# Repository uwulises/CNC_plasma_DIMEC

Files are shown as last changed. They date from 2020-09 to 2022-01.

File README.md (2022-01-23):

# Plasma CNC (LinuxCNC), Mechanical Engineering Department, Universidad de Chile [Currently on hiatus due to COVID-19].
Continuation of the development of a plasma CNC cutter.
Design based on https://www.precisionplasmallc.com/
- http://linuxcnc.org/2020/09/08/LinuxCNC-2.8.0/
- http://linuxcnc.org/docs/2.8/html/plasma/plasmac-user-guide_es.html (spanish version)
- http://linuxcnc.org/docs/devel/html/plasma/plasmac-user-guide.html

# CAD
Fusion 360 design https://a360.co/3tTwJg2

# Software
For this case, LinuxCNC V2.8 will be used, using a desktop computer with parallel port + optocoupler

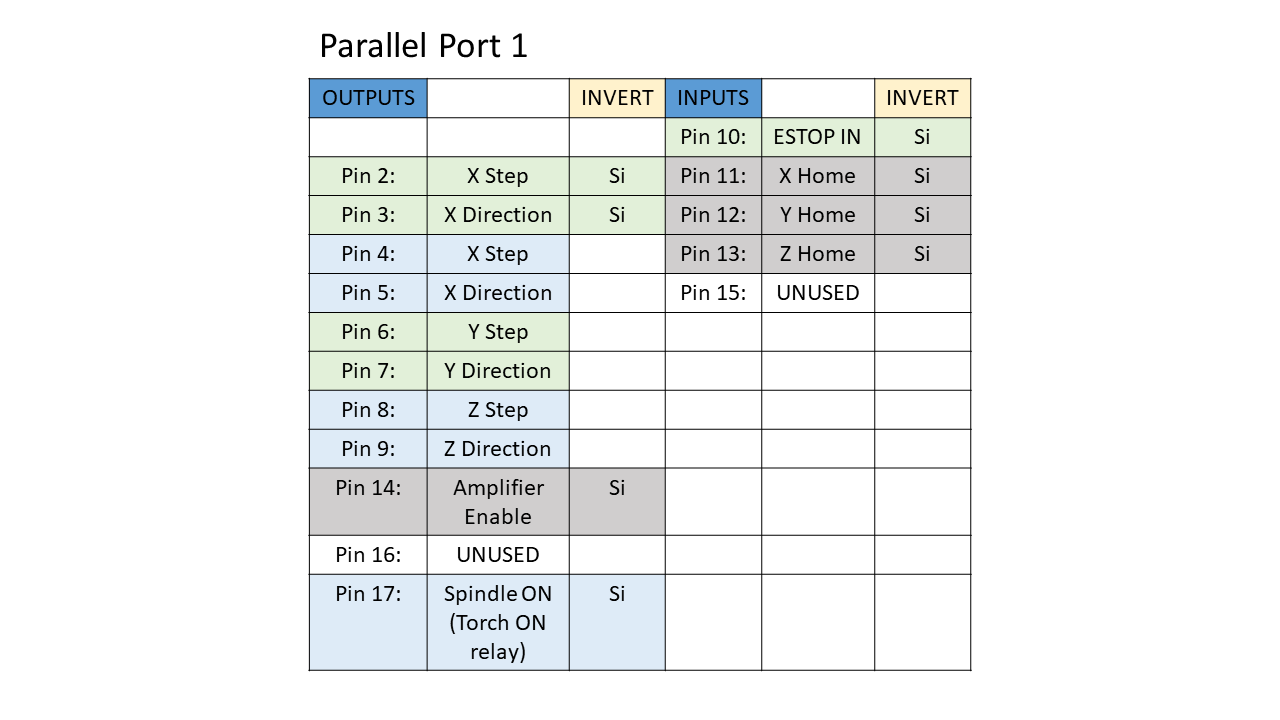
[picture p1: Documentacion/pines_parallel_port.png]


# Hardware
- Interface 5axis CNC
- Nema 23 HS45-4204S 3Nm 3A Stepper motors
- Driver DM556
- Timing Belt Pulley XL (14 & 44 teeth)
- Timing Belt 136 XL 10mm width
- Rack module 1.5 (X, Y axis)
- Gear module 1.5 20 teeth
- LJ12A3-4-Z/BX sensors (endstop)

# Electronics
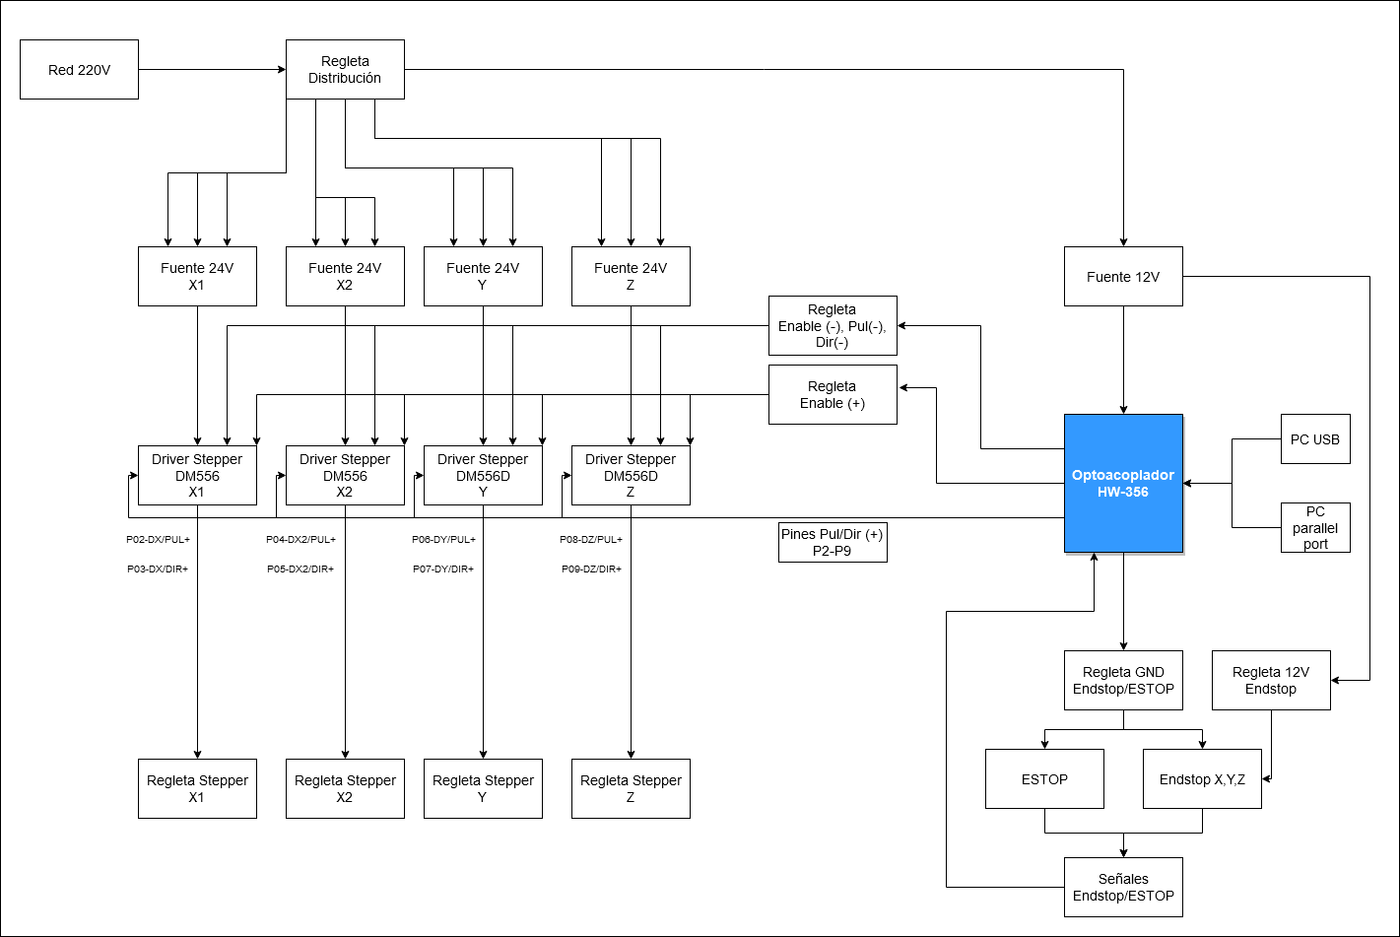
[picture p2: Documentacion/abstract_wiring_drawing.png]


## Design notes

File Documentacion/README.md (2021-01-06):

# Documentacion

- ME5601, old files from previous courses (Mechanical engineering students 2018)
- 5axis_CNC_interface, datasheet
- Informe electrico, old file from previous courses (Electrical engineering st 2018)
- Partes, BOM info

# Cableado



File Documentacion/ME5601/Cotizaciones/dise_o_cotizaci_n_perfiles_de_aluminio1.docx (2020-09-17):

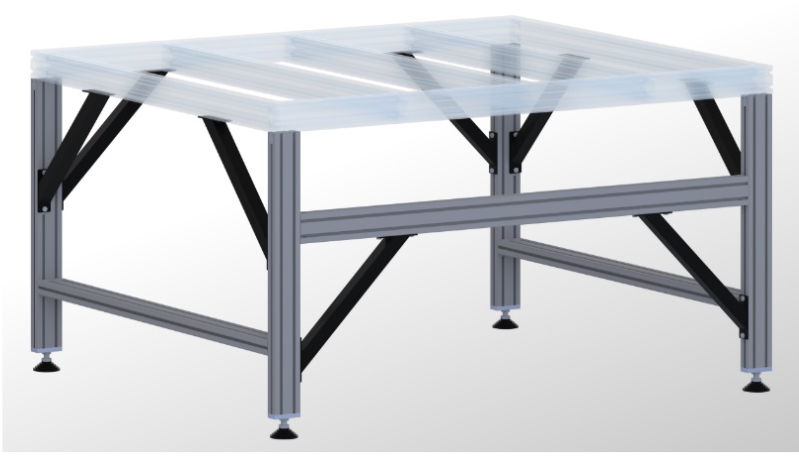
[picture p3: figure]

Cotización barras de aluminio de extrusión:

Para la mesa se consideró una forma de este tipo,con una superficie de 2,5mx2,5mx

Se encontraron 2 opciones viables, según el video: ttps://www.youtube.com/watch?v=ugjJXa6Sfl0

Para la realización de este tipo de mesa, se necesita:

N° | Pieza | dimensión | Precio [pesos] | cantidad | Total [pesos] | comentarios
1 | Marco extrusión simple 30X30mm | 30mmx30mmx1000mm | 6900 | 63 mts | 434700 | Se usan 2 barras de aluminio para mayor estabilidad en las patas como también para mayor precisión en los rieles
2 | Marco extrusión doble 20X40mm | 20mmx40mmx1000mm | 10135 | 31,5 mts | 319252,5 | Al ser doble, se puede ahorra en la cantidad de metros de material
3 | Placa unión* | variable | | 10 | | No se encontró precios de referencia, verificar precio
4 | Escuadras (union)** | 4 | 4990 | 4 | 19960
5 | Tornillo de nivelación | 4 | 1000 | 4 | 4000
6 | Barras diagonales | | aún por cotizar | 8
7 | M8 self aligning Roll-in T-nut | | 925 | 40 | 37016
8 | M8x30.00mm Socket Head Cap Screw (SHCS) | 30mm | 264,4 | 16 | 4230
9 | M6 x 14.00mm Socket Head Cap Screw (SHCS) | 14mm | 178,47 | 32 | 5711

*: Depende específicamente del diseño a utilizar, se puede hacer a la medida

**: la imagen de la escuadra es la que sigue y también se pueden realizar las uniones mediante placas adaptadas, por lo que no son del todo necesarias

Importar la mesa de 5’x10’ lista para su construcción cuesta: 874205,55 CLP (incluye costos de envío, además todas las uniones y un manual)

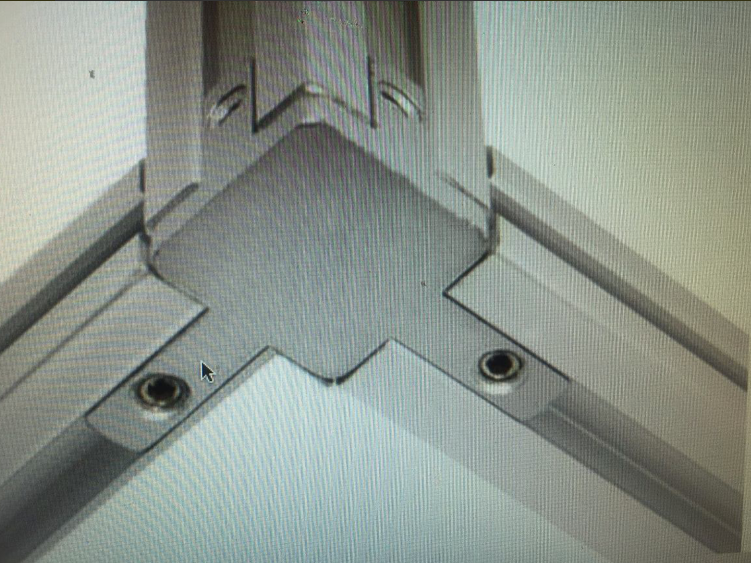
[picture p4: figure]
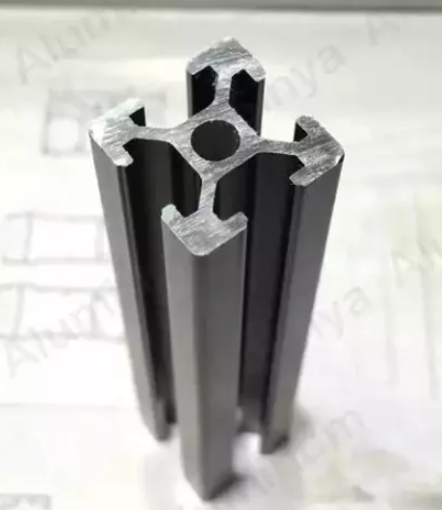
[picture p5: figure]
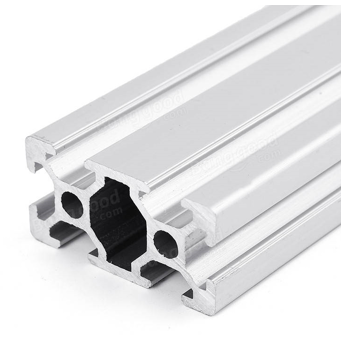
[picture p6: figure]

Figura 1. Escuadra (unión) Perfil simple Perfil Doble

Link precios marcos de extrusión:

Simple: https://articulo.mercadolibre.cl/MLC-450925992-perfil-aluminio-estructural-3030-6900-el-metro-mas-iva-_JM

Doble: https://www.banggood.com/es/Machifit-1000mm-Length-2040-T-Slot-Aluminum-Profiles-Extrusion-Frame-For-CNC-p-1264431.html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

Link detallado construcción mesa (todas sus piezas, pero otras dimensiones):

http://www.cncrouterparts.com/cad/2016Q4/CRP813-00-Leg-Kit-Plans_v2016Q4_1.pdf

Para el los tornillos con cabeza hexagonal, la cotización se realizo en :

https://8020.net/catalog/category/view/s/shop/id/837/?cat=469&p=3

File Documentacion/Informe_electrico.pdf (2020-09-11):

Universidad de Chile
Departamento de Ingeniería Eléctrica EL5004 - Taller de Diseño

# Informe Final

## CNC Plasma

### Profesores: Matías Mattamala Miguel Patiño

### Estudiantes: Juan Pablo Ruiz Felipe Salfate

Introducción | 3
Figura 1- Estructura del sistema de plasma CNC. | 3
Objetivo General | 3
Objetivos específicos | 4
Estructura del informe | 4
Especificaciones técnicas | 5
Alimentación | 5
Conexión con computador | 5
Requisitos de computador | 5
Hardware | 6
Descripción general de circuito de CNC | 6
Diagrama de módulos | 6
Consideraciones del computador | 7
Puerto paralelo | 7
Esquema de conector DB25 paralelo | 7
Tarjeta de optoacoplación de puerto paralelo de 5 ejes | 7
Pinout Tarjeta de optoacoplación de puerto paralelo | 8
Fuente de Poder | 8
Drivers | 8
Motores stepper | 9
Conmutación del Plasma | 9
Periféricos | 10
Placa de montaje | 10
Representación completa de placa de montaje | 11
Conexiones y bornes de tablero | 11
Elementos de construcción | 12
Placa de Montaje | 12
Automático | 12
Barra repartidora | 12
Bornes | 13
Regleta | 13
Riel Din | 13
Canaleta | 13
Botones de Emergencia | 14
Finales de Carrera | 14
Cableado | 14
Código de colores voltaje alto AC | 14
Código de colores voltaje medio DC | 14
Código de colores señales | 15
Conexiones y bornes de circuito en tablero | 15
Software | 16
Ejemplo de interfaz grafica de linuxCNC | 16
Instalación de Linux y Linux CNC | 16
Configuración LinuxCNC | 17
Configuraciones iniciales | 17
Valores CNC Plasma | 18
Prueba de Jitter | 19

Configuración puerto paralelo | 19
Configuración CNC Plasma | 20
Opciones de interfaz | 21
Configuracion ejes | 21
Encontrar velocidad máxima | 22
Encontrar aceleración máxima | 23
Valores CNC Plasma | 23
Uso de la interfaz | 23
Implementación y Resultados | 25
Resultados | 25
Prueba final de tablero en máquina | 25
Implementación lograda de placa de montaje | 26
Problemas | 26
Conclusiones | 27
Bibliografía | 28
Anexos | 29
Configuración Breakout Board CNC con Optoacoplación de 5 ejes | 29
Outputs de motores | 29
Inputs de señales | 29
Outputs de Señales | 30

## Introducción

El siguiente informe da cuenta del diseño y construcción realizado para la parte electrónica de la máquina CNC plasma, a ser construida en el taller Molina. Este informe tiene como objetivo dar cuenta del trabajo realizado durante el semestre, además de documentar sobre todos los aspectos del proyecto requeridos para poder ser finalizado, además de poder hacer reparaciones o modificaciones.

En la siguiente figura se puede ver el sistema implementado. Se comienza por el diseño de una pieza o corte en un sistema CAD externo cómo fusion 360 u otro, desde un equipo externo. Desde este se genera un código G, que describa la maquinación, el cual es interpretado por LinuxCNC, software instalado en la máquina que se preocupa de entregar las instrucciones a los componentes. Por medio de un cable paralelo, se envían las instrucciones a los drivers y al conmutador del plasma, pasando antes por un optoacoplador, que asegura la seguridad del computador ante una sobrecarga. Los drivers controlan los motores de la máquina, controlando así el movimiento del cabezal, mientras que el relé controla la antorcha plasma, cortando cuando sea requerido.

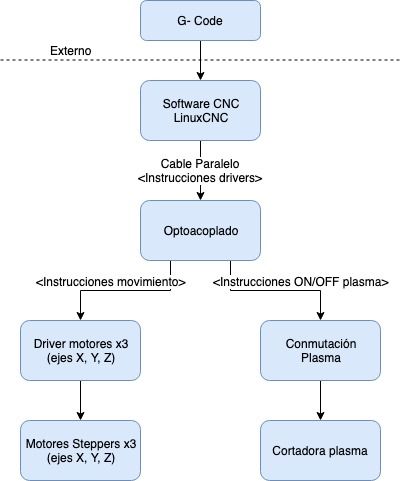
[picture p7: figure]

Figura 1- Estructura del sistema de plasma CNC.

## Objetivo General

Diseñar, implementar y testear la parte electrónica de una CNC plasma, incluyendo el control de los motores, el software CAM y los elementos electrónicos necesarios para su operación.

## Objetivos específicos

- Investigación, elección, instalación y configuración de un software CAM.
- Elección de un protocolo de comunicación entre computador y drivers.
- Diseño y construcción de tablero eléctrico, donde irán los componentes electrónicos y alimentación de la máquina.
- Diseño e implementación del cableado de la máquina.
- Testeo del correcto funcionamiento de la máquina.
- Documentación del proceso e implementación.

## Estructura del informe

Luego de introducido y el trabajo y sus objetivos, lo que sigue del informe comenzará por describir las especificaciones técnicas de diseño, seguido de distintas secciones, entregando información sobre distintos aspectos del proyecto. En la sección hardware se explicará todo lo referente al diseño e implementación de la placa de montaje. Del mismo modo, en la sección software se explicará LinuxCNC y su uso. Se continúa con los resultados obtenidos en la implementación y testeo para finalizar con un análisis del proceso y consideraciones futuras en las conclusiones.

## Especificaciones técnicas

Esta sección pretende ser un resumen de algunos aspectos técnicos importantes para una consulta más rápida del documento.

### Alimentación

El circuito se alimenta con 220 volts AC en red regular y con 5 volts DC por USB en el optoacoplador. El optoacoplador requiere ser alimentado tanto por 12V desde un transformador en la placa, como por 5V desde un cable USB.

### Conexión con computador

El optoacoplador de la placa se conecta usando un cable Db25 con un computador a través de puerto paralelo. Es importante asegurarse de que efectivamente el cable tenga todas las conexiones que debe tener, de otra manera el circuito no funciona.

### Requisitos de computador

La placa debería poder usarse con cualquier software CAM que funcione con puerto paralelo, es preferible usar un computador antiguo por temas de compatibilidad nativa. En este informe se expone el uso con LinuxCNC. Para este fin el computador debe tener un puerto paralelo instalado, una tarjeta de video para evitar retardos en el funcionamiento y linux instalado. Se expone en la sección correspondiente cómo realizar la instalación del software.

## Hardware

Se describen en esta sección todos los elementos eléctricos utilizados para el funcionamiento de la máquina. Se describe además, el diseño del tablero eléctrico implementado para la contención de todos los elementos necesarios, deteniéndose en aquellos elementos cuyo funcionamiento es importante para la operación de la máquina.

## Descripción general de circuito de CNC

El siguiente diagrama explica los módulos implementados para el funcionamiento del circuito. Existen dos tipos de conexiones importantes que tener en cuenta, las de alimentación y las de señal.

Comenzando por la alimentación del circuito, los elementos y conexiones que son de alta potencia (220V AC) están en rojo, las que son de potencia media (20-12 V DC) en amarillo y las conexiones de baja potencia (5 V DC) son verdes. Hay dos detalles importantes que tener en cuenta, en la etapa de alimentación de alta potencia, la fase pasa por un automático y un interruptor de emergencia, cosa de poder detener el circuito a tiempo en caso de cualquier problema. Además, el optoacoplador si bien tiene un puerto USB que debe ser conectado a una fuente para tener 5 V de referencia, no recibe la energía de ahí. Tiene su transformador propio de 12 volts con el cual se energiza.

Los nodos internos de control están en azul, las señales externas en blanco y los periféricos controlables en gris. El optoacoplador recibe señales desde los interruptores y el cable paralelo y envía señales hacia los drivers que controlan los motores, además de contar con un relé que puede ser usado para la conmutación del plasma. Los interruptores son energizados directamente desde el optoacoplador.

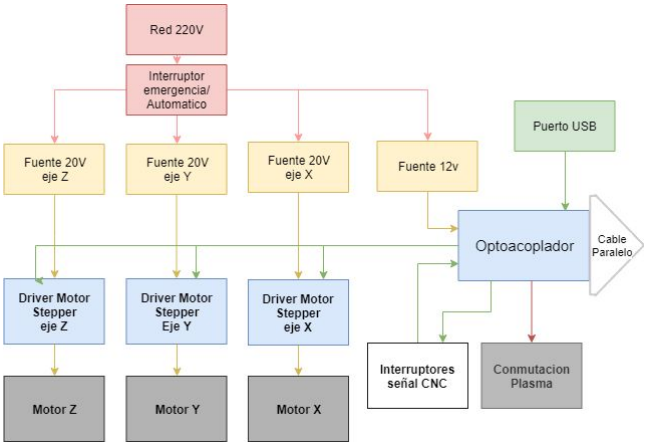
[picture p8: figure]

Diagrama de módulos

### Consideraciones del computador

LinuxCNC pide 2 elementos base para su funcionamiento, el primero es la presencia de un puerto paralelo, ya sea nativo o mediante una tarjeta, y el segundo es la presencia de una tarjeta de video para liberar de carga al procesador utilizado. En general el software va a funcionar mejor en computadores antiguos, además de requerir menos modificaciones (por lo general los computadores antiguos tenían puerto paralelo nativamente, cosa que ha desaparecido en los últimos años).

El sistema operativo elegido para operar es Linux, esto es importante por 3 razones. La primera suena bastante obvia, pero vale recalcar que LinuxCNC solo funciona en linux. Linux a diferencia de Windows es un sistema donde se permite nativamente la ejecución en tiempo real, en windows softwares cómo Mach3 necesitan driver especiales, que suelen tener conflictos con los computadores más modernos. Además, al ser un sistema altamente configurable, el desempeño de Linux en los computadores antiguos es bastante más fluido que el que puede tener Windows.

### Puerto paralelo

El puerto paralelo consiste en 25 canales de comunicación bidireccional, teniendo canales de entrada, salida y tierra, que pueden ser usado para la comunicación con periféricos por medio de un puerto PCI. Antiguamente era el medio estándar para la comunicación con impresoras, sin embargo el USB quitó su lugar, al ser más cómodo y barato. Pese a esto, el USB es solo comunicación serial, siendo más lento que el cable paralelo, teniéndose que en máquinas CNC, la velocidad de comunicación es clave.

Para la conexión de linuxCNC con cualquier máquina CNC, se requiere de un cable de puerto paralelo DB25. Es inmensamente importante tener cuidado al momento de comprar el cable, comprobando que efectivamente sea un DB25, el cual tiene todas sus pines conectados. Es más común encontrar cables de impresora que trae varios pines sin conexión, no siendo necesarios para el control de impresoras, abaratando costos en el proceso.

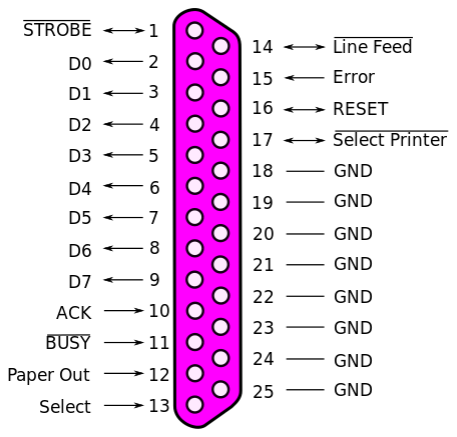
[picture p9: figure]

Esquema de conector DB25 paralelo

### Tarjeta de optoacoplación de puerto paralelo de 5 ejes

Se hizo uso de una tarjeta idéntica a la de la figura para la optoacoplación . Esta se conecta al

1
computador mediante un conector DB25 y se alimenta mediante USB. Se puede alimentar con una fuente de 12 a 24V, sin embargo se sigue requiriendo la conexión USB para funcionar. Permite transmitir hacia el computador 5 señales, siendo parada de emergencia y límites de ejes X, Y y Z, y desde el computador, las señales de control de hasta 5 drivers, un control optoacoplado de motor de

1 Se trata de un modelo Chino del cual la documentación es difusa, pero se adjunta en anexos.

hasta 10 volts en PWM (solo si recibe alimentación extra) y un relay configurable mediante un jumper. En caso de que se configure el relé, el eje B (5to eje) no puede ser usado.

Según el manual del optoacoplador, la conexión del relé se hace en el pin de B Dir, sin embargo en algunos lugares se menciona que esto debe ser realizado en la interfaz ON/OFF del Spindle. La conexión correcta no pudo ser corroborado.

Pinout Tarjeta de optoacoplación de puerto paralelo

### Fuente de Poder

Todas las fuentes escogidas son switching de voltaje constante. Se tienen 3 de 20 Volts para los drivers y 1 para el optoacoplador. Este último, si bien obtiene su energía en mayor parte de la fuente de poder, debe ser conectado por USB a un computador para tener 5 Volts de referencia. La falta de esto deja a la fuente sin la polarización necesaria para operar correctamente, e inhibe el correcto funcionamiento del circuito. En aplicaciones de poca potencia es posible usar el optoacoplador solo haciendo uso del USB, dejando a la fuente de 12 volts cómo opcional.

En cuanto a los drivers, se usa una fuente de poder para cada eje, cosa de asegurar mayor robustez ante los fallos. El uso de solo una fuente podría funcionar bien en aplicaciones de poca potencia, pero en las pruebas con un stepper nema 23 se llegó a ver voltajes cercanos a los 100 volts en la salida del driver, cosa que prueba la potencia que puede llegar a exigir ciertos motores.

### Drivers

Para poder controlar un motor stepper se pueden utilizar drivers especializados para ello. Con el driver se puede controlar la intensidad, dirección y habilidad o desabilidad el motor, además de poder conseguir una mayor definición de giro con micro-pasos.

El driver recibe como entrada 3 señales, Dir, Pul y Enable. Con Dir se controla la dirección de giro del motor, con Pul se envía un tren de pulsos según los cuales gira el motor y Enable sirve como un pin de control.

El driver recibe la alimentación de los motores y la conexión con los ejes A y B del motor, con los cuales puede energizar y controlar el motor.

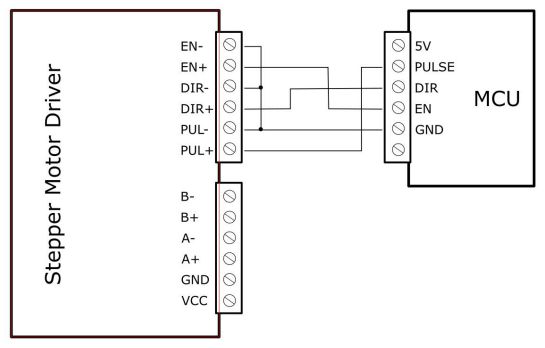
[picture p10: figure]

Al conectar el driver existen 2 configuraciones, ánodo común, en donde todos los polos positivos de control se conectan juntos a un voltaje positivo, y cátodo común, en donde todos los polos negativos de control se conectan a tierra. Los polos opuestos se conectan a las respectivas señales de Dir, Pul y Enable. Las características producto del tipo de conexión que se haga dependerá del driver que se esté utilizando.

Los drivers a utilizar en la versión final son los DM556, sin embargo, debido a que no se contó con su disponibilidad, se utilizó el driver DM860 para las pruebas.

### Motores stepper

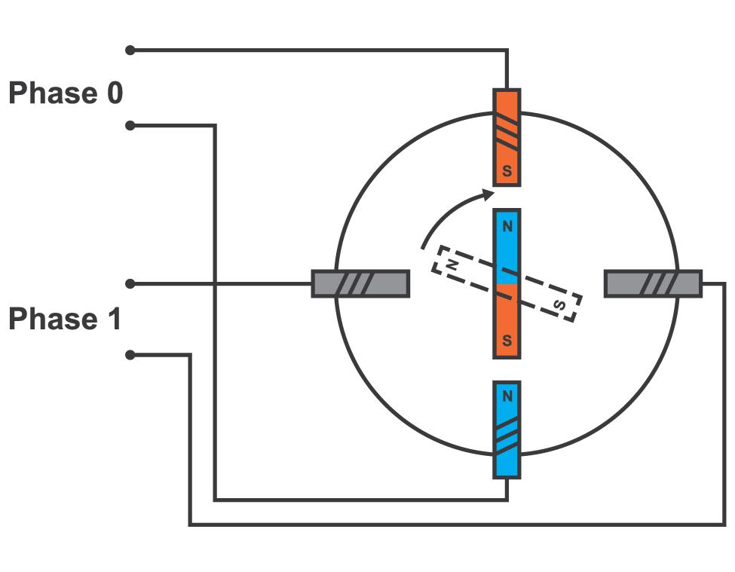
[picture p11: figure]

Consiste en una serie de electroimanes, excitados por bobinas, que controlan la posición de un eje magnético, siendo generalmente bipolares (2 electroimanes). Al energizar una bobina un electroimán se activará, con la orientación dependiendo del sentido de la corriente. Según cuales y en qué sentidos se activen los electroimanes se cambiará la posición del eje. Finalmente encadenando una serie de estos movimientos se consigue que el eje gire. Que estas rotaciones sean discretas hace que estos motores sean muy precisos, lo cual resulta útil para ciertas aplicaciones como lo son el control de máquinas CNC.

El motor a utilizar es un motor Nema23. Pese a que las pruebas fueron realizadas con este motor, no eran los comprados para la máquina.

### Conmutación del Plasma

Con respecto a la conmutación del plasma, esta depende del modelo de antorcha que se compre, sobre la cual lamentablemente de momento no hay claridad. Es posible que se pueda usar el Relay que trae la placa de optoacoplación para la conmutación de este, sin embargo hasta tener el modelo definitivo no se tienen claridad.

### Periféricos

Los periféricos se conectan directamente a la tarjeta de optoacoplación, estos comparten una misma tierra y tienen diferentes entradas. Hay una recomendación por parte del fabricante de la tarjeta sobre para qué usar los puertos sin embargo, el uso de estos es configurable cómo se verá en la sección correspondiente. Mecánicamente pueden ser botones y fines de carrera cómo los que se muestran en la sección de elementos de construcción.

Para los finales de carrera, existen 2 tipos de switch, aquellos que están normalmente abiertos y otros que están normalmente cerrados. Considerando que se debe enviar una señal en el momento en el que uno de estos switches es cerrado, existen 2 configuraciones. Para los switches normalmente abiertos, se deben conectar en paralelo, en el momento en el que uno de estos es presionado, se cierra el circuito y envía la señal.

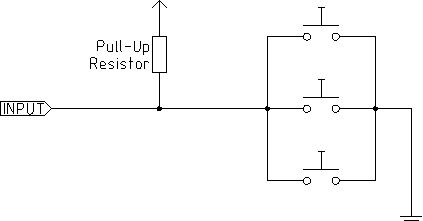
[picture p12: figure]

Para los switches normalmente cerrados, se deben conectar en serie, en el momento en el que uno de ellos es presionado, el circuito es abierto, enviando la señal.

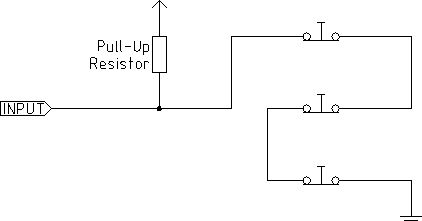
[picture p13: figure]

## Placa de montaje

Los elementos fueron instalados en una placa de montaje de diseño idéntico al de la figura. Se adjunta una versión en tamaño completo al final del informe y en bibliografía los archivos fuente. Importante notar que al momento de escrito este informe ni los drivers ni los transformadores de 20 volts habían sido montados, a la espera de encontrar los modelos que iba a ser usados finalmente en la máquina CNC.

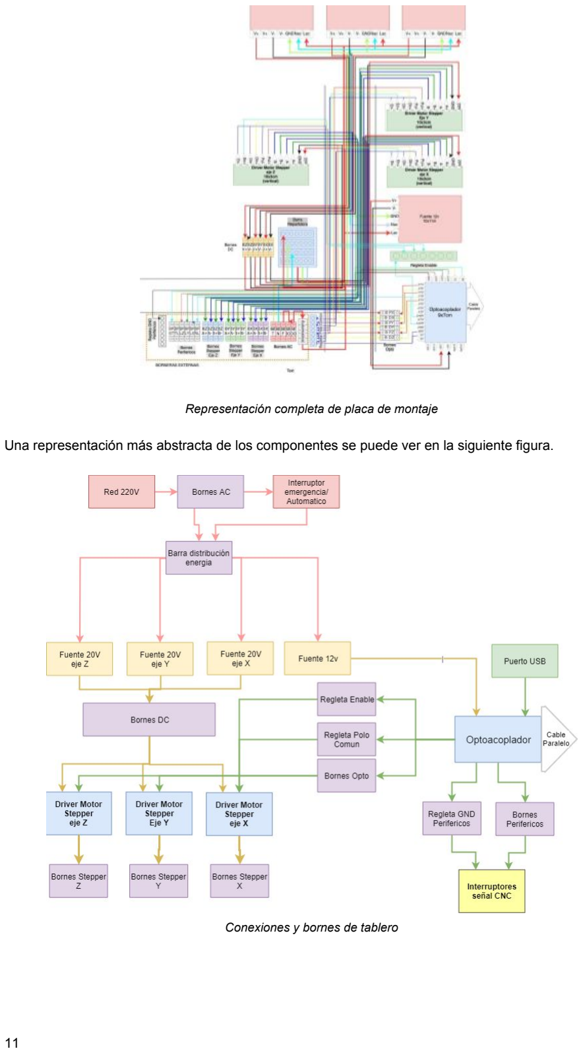
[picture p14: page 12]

Representación completa de placa de montaje

Una representación más abstracta de los componentes se puede ver en la siguiente figura.

Conexiones y bornes de tablero

### Elementos de construcción

Placa de Montaje

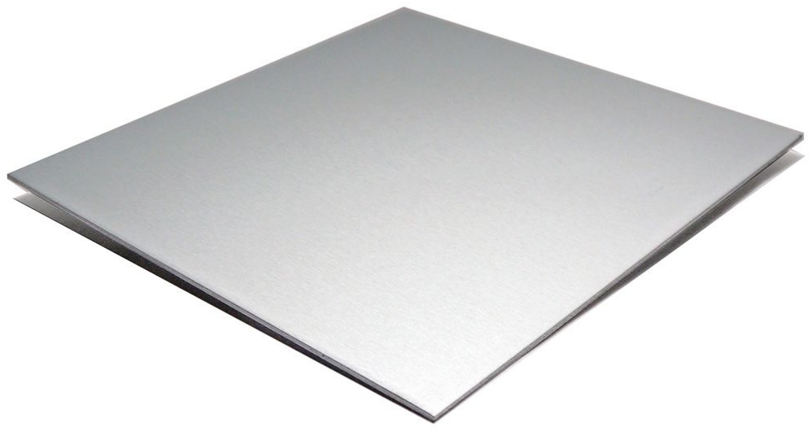
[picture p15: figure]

La placa de montaje utilizada fue una placa de aluminio de 500x500x1mm. Fue comprada en Maquimetal ltda, ubicada en Obispo Manuel Umaña 791, Estación Central (cerca del metro Universidad de Santiago).

Automático

Se utilizó un automático monofásico de 32A, conectada a la fase de 220V AC.

Barra repartidora

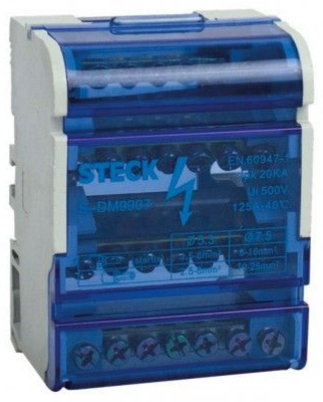
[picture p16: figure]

Para los nodos de fase, neutro y tierra de 220V AC, con los cuales se alimentan las fuentes de poder de los motores y del optoacoplador de 5 ejes, se utilizó un repartidor tetrapolar.

Bornes

Para las conexiones uninodales entre elementos del tablero y para conexiones externas con el tablero se utilizarán bornes. Se utilizaron 3 tipos de bornes, bornes de 6mm para los voltajes altos AC, bornes de 4mm para los voltajes medios DC y bornes de 2mm para señales.

Regleta

Para las conexiones multi-nodales se utilizaron regletas. En este caso correspondió a las señales enable y de polo común de los driver, y para la tierra común de las señales externas.

Riel Din

Para la colocación de los bornes y regletas, además del automático y barra repartidora, se utilizaron rieles Din perforados.

Canaleta

Para esconder y proteger el cableado del tablero se utilizaron canaletas ranuradas de 10x6cm.

Botones de Emergencia

Aún no han sido comprados, sin embargo dentro del diseño se contemplan 2 botones de emergencia. Uno de ellos corta directamente la corriente de la alimentación, mientras que el segundo envía una señal de parada de emergencia al optoacoplador.

Finales de Carrera

Aún no han sido comprados y no corresponde a elementos dentro del tablero, los finales de carrera son elementos importantes en la parte electrónica del CNC plasma. Estos son botones que indican los límites de de cada eje de la máquina, siendo un total de 6. Al ser presionados envían la señal que se llegó al límite, deteniendo las máquinas automáticamente.

### Cableado

Para las conexiones se utilizaron 3 tipos de cables:
➔ Cable de 6mm de diámetro para voltaje alto AC, correspondiente a alimentación de fuentes de poder.
➔ Cable de 4mm de diámetro para voltaje medio DC, correspondiente a alimentación de drivers, motores y optoacoplador.
➔ Cable de 1.5mm de diámetro para señales.

Además, se utilizó un código de color para las conexiones, considerando que en las tiendas generalmente se dispone de 6 colores diferentes. El código de colores para el AC es el estándar, sin embargo para las bobinas y las señales en general este puede ser cambiado. También se recomienda cambiar el ancho de los cables, considerando que están sobredimensionados.

Código de colores voltaje alto AC
- Rojo: Fase 220V AC
- Blanco: Neutro 220V AC
- Verde: Tierra 220V AC

Código de colores voltaje medio DC
- Rojo: Voltaje positivo DC
- Negro: Voltaje negativo DC
- Verde: Bobina positiva motor
- Azul: Bobina negativa motor

Código de colores señales²
- Rojo: Señales Pul y limitador eje X.
- Amarillo: Señales Dir y limitador eje Y.
- Blanco: Señales Enable, parada de emergencia y relé conmutador plasma.
- Negro: Tierra común señales externas.
- Azul: Polo común driver y limitador eje Z.
- Verde:Señal Tool Setting.

### Conexiones y bornes de circuito en tablero

En el siguiente diagrama se exponen los bornes y conexiones. Se adjunta en anexos una versión sin pérdida de este diagrama. Nótese que los colores de los cables en general son los colores usados finalmente en el tablero y no representan valores de voltajes cómo en los diagramas anteriores.

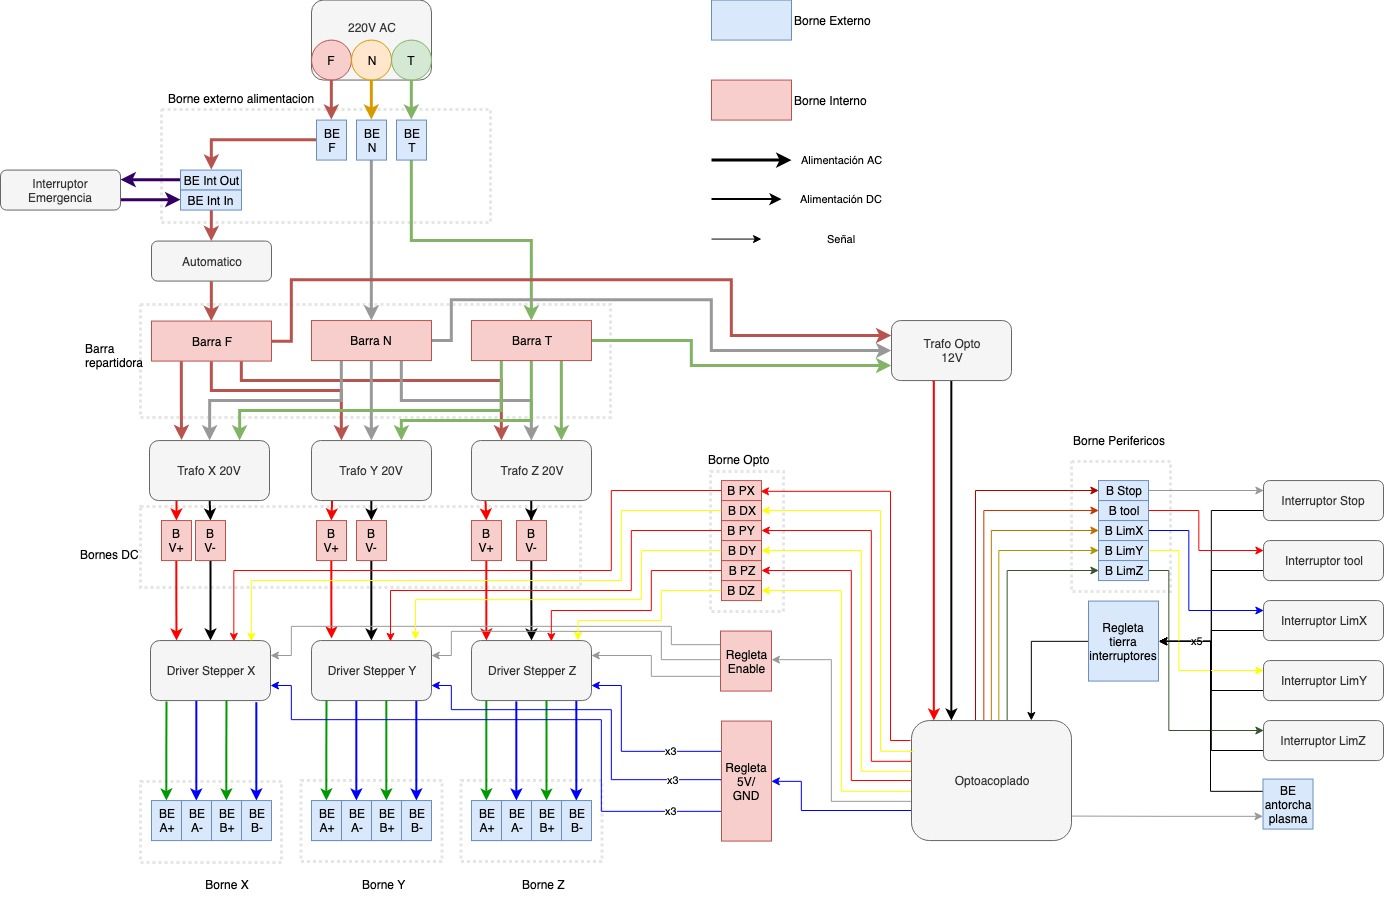
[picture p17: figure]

2 Con respecto a las señales periféricas, siendo estas limitadores ejes X, Y, y Z, junto con la señal de emergencia y relé plasma, lo importante es que en lo posible queden de distintos colores.

## Software

LinuxCNC (http://linuxcnc.org/) es un software opensource CAM que permite operar una máquina CNC directamente desde el computador. Es de código completamente gratuito y abierto mediante licencia GNU GPLV2, además, está hecho y mantenido por una comunidad bastante activa. No tiene herramientas CAD ni de generación de g-Code, solamente lee instrucciones generadas externamente y las transmite directamente.

Al ser de código abierto, permite operar virtualmente todo tipo de máquina, sin embargo las que están actualmente implementadas son variadisimas, yendo desde impresoras 3Ds a cortadoras laser. Puede operar con distintos tipos de puertos de comunicación, siendo el puerto paralelo el más usado y habiendo problemas con USB por temas de retardo propios del hardware. Además, cuenta con distintas interfaces gráficas, las cuales son configurables en código fuente, pudiéndose usar desde con computadores tradicionales a interfaces táctiles.

Funciona mejor en arquitecturas x86, preferentemente en Linux usando kernel en tiempo real. Siendo ideal para este fin el uso de computadores antiguos. Usa archivos .gcode para las instrucciones de la maquinación y .hal para la configuración.

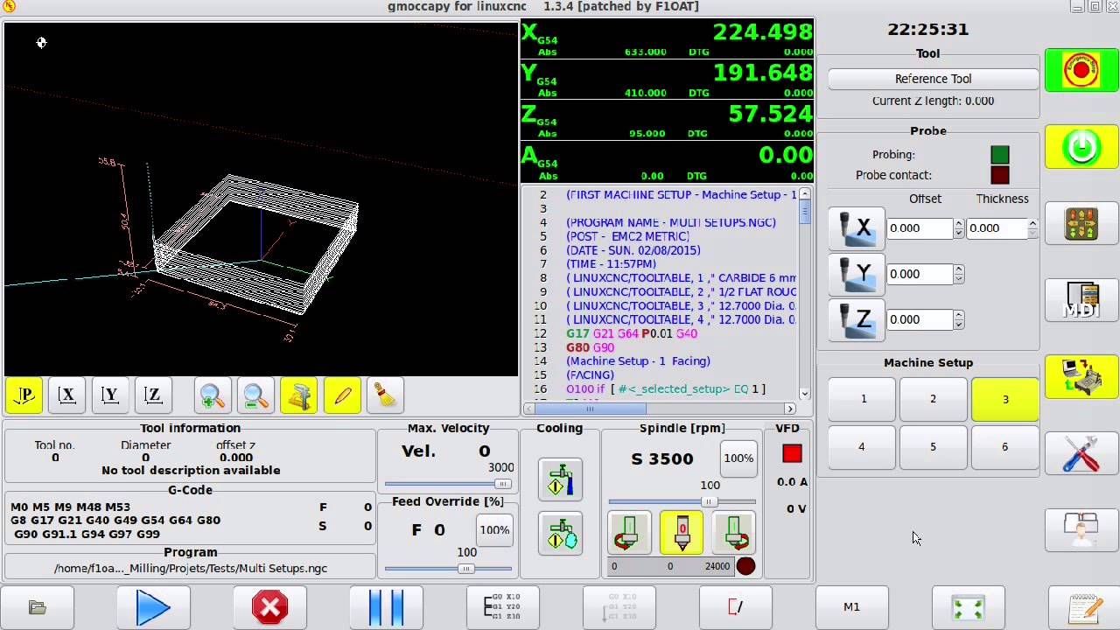
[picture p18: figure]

Ejemplo de interfaz grafica de linuxCNC

## Instalación de Linux y Linux CNC

Linux se puede instalar de manera fácil usando una imagen de un liveCD descargada desde alguna distribución como por ejemplo ubuntu en la pagina https://ubuntu.com/download. Una vez descargado el sistema debe ser booteado desde el CD, DVD o pendrive en el que la imagen fue quemada. Importante tener cuidado con el medio en el que se graba el liveCD, es posible que los computadores antiguos no permita bootear desde USB, así como también que los más modernos no tengan lector de CDs o DVDs. Desde ahí, la instalación de linux es cosa de seguir el menú o incluso es posible realizar algunas tareas básicas para probar el SO directamente en el liveCD. Para instalar linuxCNC una vez instalado linux es necesario seguir los pasos mostrados en http://linuxcnc.org/downloads/, donde se puede instalar desde la consola o bien descargar un archivo instalable .deb para los sistemas basados en debian o dpkg para otros.

La forma más sencilla sin embargo es descargar la imagen de linux con LinuxCNC previamente instalado que ofrece la pagina http://linuxcnc.org/downloads/. Si el medio escogido para quemar la imagen es en disco tener cuidado con que el peso de la imagen es de sobre 1 gigabyte, por lo que no será posible grabarlo en un CD tradicional y será necesario contar con lector de DVD.

## Configuración LinuxCNC

La configuración de la máquina se realiza en el programa Stepconf Wizard, que es instalado junto a LinuxCNC. Una vez realizada esta configuración se puede comenzar a utilizar LinuxCNC. Los archivos generados con la configuración son directamente guardados en el directorio linuxcnc/config, y para ser editados se debe escoger el archivo con extensión .stepconf en el mismo programa.

La información entregada en esta sección, además de las imágenes usadas aquí se pueden encontrar en http://linuxcnc.org/docs/html/config/stepconf.html.

Al abrir el programa aparecerá la siguiente ventana. Se recomienda usar la resolución original (800x600):

Aquí se puede escoger entre crear una nueva configuración, modificar una configuración existente o importar la configuración desde un archivo Mach, usado en el programa CNC Mach 3/4.
Se puede escoger crear un acceso directo en el escritorio del archivo de configuración, crear un acceso directo de LinuxCNC con la configuración creada/editada y crear una simulación del hardware.

### Configuraciones iniciales

Una vez escogido crear o editar una configuración y presionado Forward/siguiente, aparecerá la siguiente ventana:

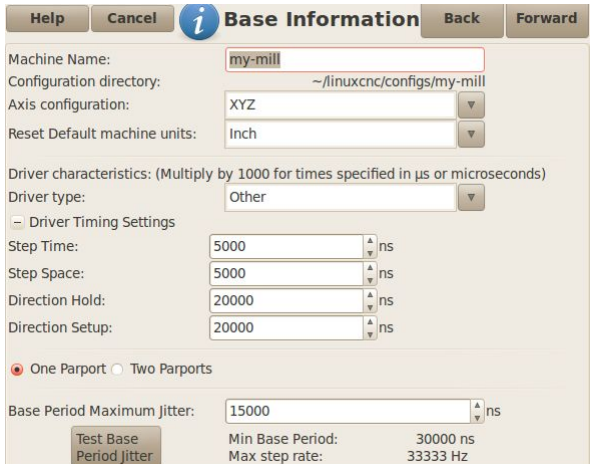
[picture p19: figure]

Aquí se puede definir:
➔ Nombre de la máquina.
➔ Los ejes de la máquina: XYZ para fresadoras, XYZA para fresadoras de 4 ejes y XY para tornos.
➔ Unidades de la máquina, siendo milímetros o pulgadas. Se escogió milímetros (mm).
➔ Tipo de driver: Si los drivers que se están ocupando aparecen aquí no se requiere configurar el timing de los drivers. Si no está, se debe escoger otros y definir las siguientes características:
◆ Step Time: Tiempo que un pulso permanece prendido (ns).
◆ Step Space: Tiempo mínimo entre cada pulso (ns).
◆ Direction Hold: Cuanto tiempo se mantiene el pin dir después de un cambio de dirección (ns).
◆ Direction Setup: Tiempo de cambio de dirección después del último pulso (ns).
Si no se está seguro de alguno de estos valores se recomienda usar 20.000 ns.
➔ Número de puertos paralelos a usar.
➔ Jitter máximo del computador: Este número corresponde a cuanto se demora el computador para responder una petición externa y se puede determinar con un test.

### Valores CNC Plasma

Los valores utilizados fueron:

-Axis Configuration: | XYZ
-Rest Default machine units: | millimeters
-Driver Type: | Other
-Step Time: | 20000 ns
-Step Space: | 20000 ns
-Direction Hold: | 20000 ns
-Direction Setup: | 20000 ns
-Número de puertos: | One Parport

Prueba de Jitter

Para poder determinar el Jitter máximo del computador se debe presionar en Test Base Maximum Jitter. Al hacer esto se abre la siguiente ventana:

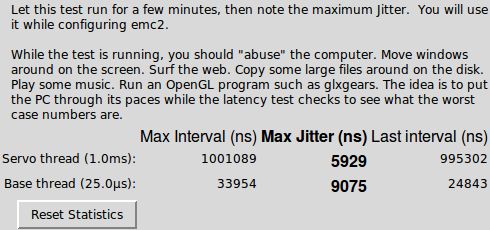
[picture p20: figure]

Al abrir esta ventana, se debe realizar una prueba de estrés en el computador, abriendo múltiples ventanas y aplicaciones, páginas web, etc. Luego de esto se debe ver el máximo jitter registrado, mostrado en la ventana, y poner ese número en la configuración.

Si el valor es menor a 20 us (20.000 ns) significa que el computador presentará buenos resultados. Entre 30 y 50 us sigue siendo bueno, pero si supera los 100 us el computador no es apto para softwares de stepping. Si el valor supera el 1 ms entonces el computador no es apto para LinuxCNC en general.

### Configuración puerto paralelo

Luego de configurado las características generales, aparecerá la siguiente pantalla:

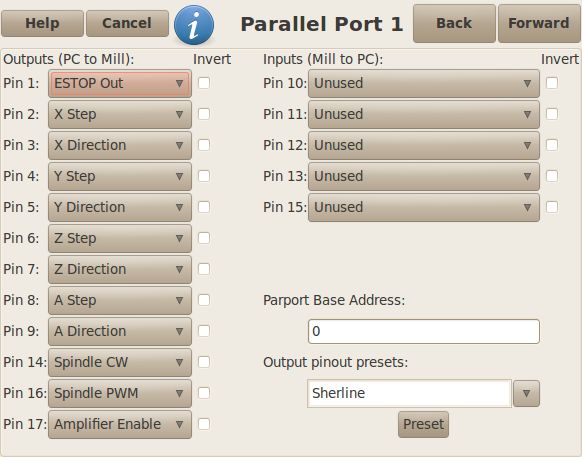
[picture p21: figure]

Aquí se configura el puerto paralelo. Se define cada pin de entrada y salida, y la dirección del puerto paralelo en notación hexadecimal. Se puede escoger si las señales de los pines van invertidas o no. También se pueden escoger configuraciones predefinidas de acuerdo a estándares existentes.

La definición de estos pines dependerá de los componentes utilizados, incluyendo si estas señales deben ir invertidos o no.

Generalmente la dirección del puerto paralelo es 0x378, sin embargo se puede ver esta dirección con
“cat /proc/ioports | grep parport”, útil en caso de utilizar otro puerto paralelo. Al ingresar este comando
aparecerá un lista con los puertos, siendo los primeros 4 de cada puerto la dirección de este (se puede ver que el puerto 0 parte con 0378). Como deben estar en notación decimal se debe agregar al principio “0x”.

### Configuración CNC Plasma

Para el optoacoplador de 5 ejes utilizado en esta máquina se tiene la siguiente configuración, que puede ser vista en su manual de usuario o en el anexo:

Número de Pin | Señal | Tipo de señal | Invertido
1 | Spindle ON | output | Si
2 | X Step | output | No/Si
3 | X Direction | output | No/Si
4 | Y Step | output | No/Si
5 | Y Direction | output | No/Si
6 | Z Step | output | No/Si
7 | Z Direction | output | No/Si
8 | - | output | -
9 | - | output | -
10 | EStop In | input | No
11 | Tool In | input | No
12 | Both Limit X | input | No
13 | Both Limit Y | input | No
14 | Amplifier Enable | output | Si
15 | Both Limit Z | input | No
16 | - | output | -
17 | Output 0 | output | No

Si se invierte la señal de los ejes dependerá de qué tipo de conexión existe. Si es cátodo común entonces va sin inversión, pero si es ánodo común entonces la señal va invertida. Las pruebas realizadas fueron con cátodo común, sin embargo funcionó con la señal enable invertida. Se debe probar si con ánodo común tiene que seguir invertida o tiene que estar sin invertir.

Para las señales de límite (12, 13 y 15), también se pueden configurar para que sean las señales del homing, para poder determinar el inicio de la antorcha.

### Opciones de interfaz

Luego de configurado los pines del puerto paralelo, aparecerá la siguiente ventana, en donde se pueden configurar opciones adicionales para la interfaz:

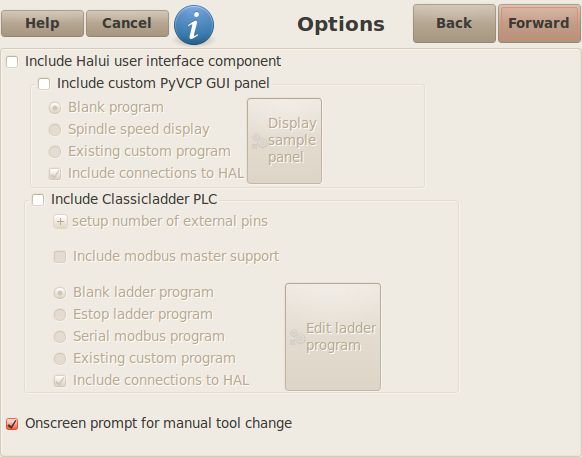
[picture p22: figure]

En general no se requiere agregar ninguna de estas opciones para hacer funcionar el programa, siendo configuraciones para agregar funciones más personalizadas dentro de la interfaz. Si se quiere saber más sobre esto se puede revisar la guía de Stepconfig de LinuxCNC.

### Configuracion ejes

Luego de configurar las opciones de interfaz, aparecerán las siguientes ventanas para los ejes X, Y y Z:

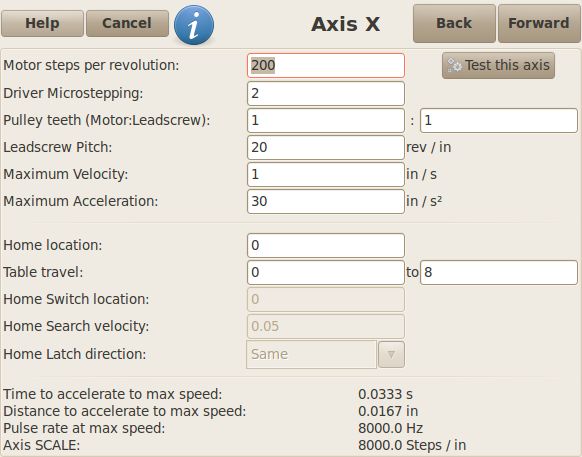
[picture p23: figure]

Las configuraciones que se deben realizar aquí son:
➔ Motor steps per revolution: Número de pasos del motor requeridos para realizar una revolución .Depende del motor. Si no aparece directamente en el datasheet se puede calcular a partir del ángulo por revolución, dividiendo 360 por dicho ángulo.

➔ Driver Microstepping: MicroStepping realizados por el driver. Si este indica el número de pulsos por revolución se debe dividir ese número por el número de pasos por revolución del motor.
➔ Pulley teeth: Razón de poleas entre el motor y tornillo, si existe. De no tener se deja en 1:1. ➔ Lead Screw Pitch: Paso del tornillo/cremallera (ancho del hilo).
➔ Maximum Velocity: Velocidad máxima del eje. Esto dependerá del motor y del tornillo. La mejor forma de determinar este valor es por medio de pruebas.
➔ Maximum Acceleration: Aceleración máxima del eje. Al igual que la velocidad depende del motor y el tornillo, y se determina por medio de pruebas.
➔ Home location: Coordenada de la posición inicial de la máquina. En caso de no tener switches que indiquen esta posición se debe mover la máquina a dicha posición antes de apretar el boton de Home.
➔ Table travel: Límites del eje. La posición del Home no debe ser igual a uno de estos límites.

En caso de haber definido los switchs del Home en la configuración del puerto paralelo se habilitarán las siguientes configuraciones:

➔ Home Switch location: Posición relativa en donde se libera el switch del Home. En caso de usar el switch de límite como switch del Home, su posición debe ser distinta del Home.
➔ Home Search velocity: Velocidad con el que buscará el switch del Home. Si este está en el límite, la velocidad debe ser tal que sea capaz de desacelerar al llegar al switch.
➔ Home Latch direction: Determina la dirección del switch. Same define el Home cuando aprieta el switch 2 veces, Opposite define el home cuando suelta el switch.

En este menú también se puede controlar directamente el motor, pudiéndose probar si la configuración fue realizada correctamente, además de determinar la velocidad y aceleración máxima. Para eso se debe presionar en Test this axis, abriéndose la ventana que se ve abajo. Aquí se puede definir a qué velocidad y aceleración se moverá el motor. Se puede mover manualmente en ambas direcciones, o definir que se mueva automáticamente dentro de un área.

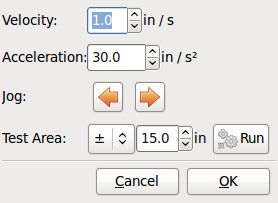
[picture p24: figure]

### Encontrar velocidad máxima

Para determinar la velocidad máxima, se debe escoger una aceleración baja (50 mm/s ) y un área

2
segura en la cual se debe mover el eje. Luego se coloca la máquina en el centro, se coloca la velocidad máxima que se espera conseguir y se aprieta Run. Si durante el proceso el motor no presenta detenciones significa que puede trabajar en dichas velocidad, de lo contrario, se debe bajar la velocidad.

Una buena forma de verificar que no hubo detenciones es volver a presionar Run, esto hará que el motor retorne a su posición original, si este está corrido del original significa que en efecto el motor se detuvo durante pequeños intervalos de tiempo.

Se recomienda reducir en 10% la velocidad máxima encontrada para la configuración.

Al realizar esta prueba se debe asegurar que se llegue a la velocidad. Para saber si el rango de movimiento es el suficiente se puede utilizar la siguiente ecuación:
d = 0.5 a

V

2

### Encontrar aceleración máxima

La búsqueda de la aceleración máxima se realiza de la misma forma que la velocidad máxima, cerciorándose nuevamente que el área escogida es suficiente para alcanzar la velocidad máxima.

### Valores CNC Plasma

Debido a que no se contaban con todos los componentes, ni se pudieron hacer pruebas en la mesa, los valores utilizado en las pruebas no son útiles para la CNC plasma.

## Uso de la interfaz

LinuxCNC tiene una serie de interfaces que pueden ser utilizadas. La interfaz utilizada en este proyecto fue Axis, mostrada a continuación:

Por defecto la maquina se encuentra apagada. Se enciende apretando el botón verde o F2. Si el cabezal no sobrepasa ninguno de los límites, y si ninguno de los finales de carrera o botón de emergencia se encuentra presionado, entonces la máquina se prendera. Si alguno de estas condiciones se cumple la máquina automáticamente enviará un mensaje de error y se apagará. Del mismo modo se puede presionar el botón rojo o F1 para activar la parada de emergencia.

En Axis se puede cortar un modelo a partir de un archivo, o controlar cada uno de sus ejes de forma independiente.

Para el control manual se encuentra el menú de ejes en F3. Aquí se puede controlar el eje en una dirección u otra, además de dejar el cabezal en el Homing del respectivo eje, necesario para ejecutar un archivo. Segun se haya configurado, este considerará como home la posición inicial o lo buscara yéndose a los extremos. El primer caso se da cuando se tiene configurado un homing manual, en ese caso uno es el responsable de mover el cabezal a la posición inicial de forma manual.

Para ejecutar un archivo se tienen 4 botones, siendo el de ejecutar, pasar a la proxima linea, pausar o detener la ejecución el programa.

Axis muestra el modelo que se desea cortar, y se muestra en tiempo real el avance de la máquina. Además se tienen botones con lo que se puede cambiar la vista de dicha ventana, además se puede arrastrar el mouse para cambiar la vista de forma manual, utilizando la rueda para acercar o alejar la vista.

Una guía más detallada puede ser encontrada en http://linuxcnc.org/docs/html/gui/axis.html.

## Implementación y Resultados

## Resultados

Para las pruebas se utilizaron componentes de otra maquina, al no contar con los componentes reales del CNC plasma. Se logró controlar de manera correcta un motor y moverlo utilizando LinuxCNC, cortando un modelo predefinido del software. Esto da como resultado del correcto control de los 3 ejes, siendo el control de los otros ejes análogo al eje controlado. Fue posible además realizar pruebas de la detención de emergencia e interruptores de final de carrera, y comprobar su correcto funcionamiento.

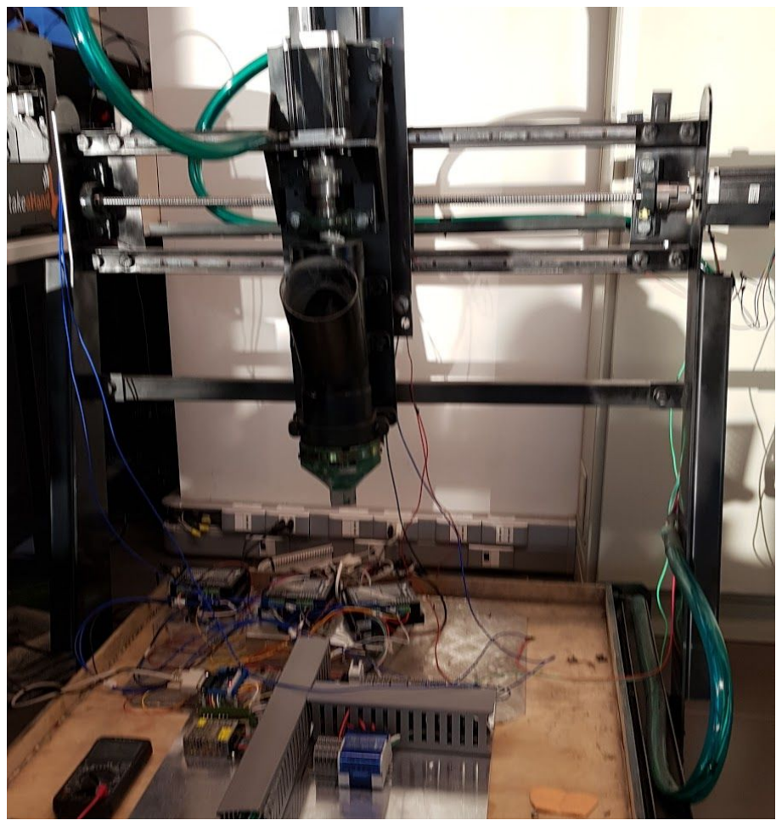
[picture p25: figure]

Prueba final de tablero en máquina

La implementación final de la placa de montaje es la que se ve en la siguiente imagen. Se decidió no incluir los transformadores de los drivers ni los drivers para evitar

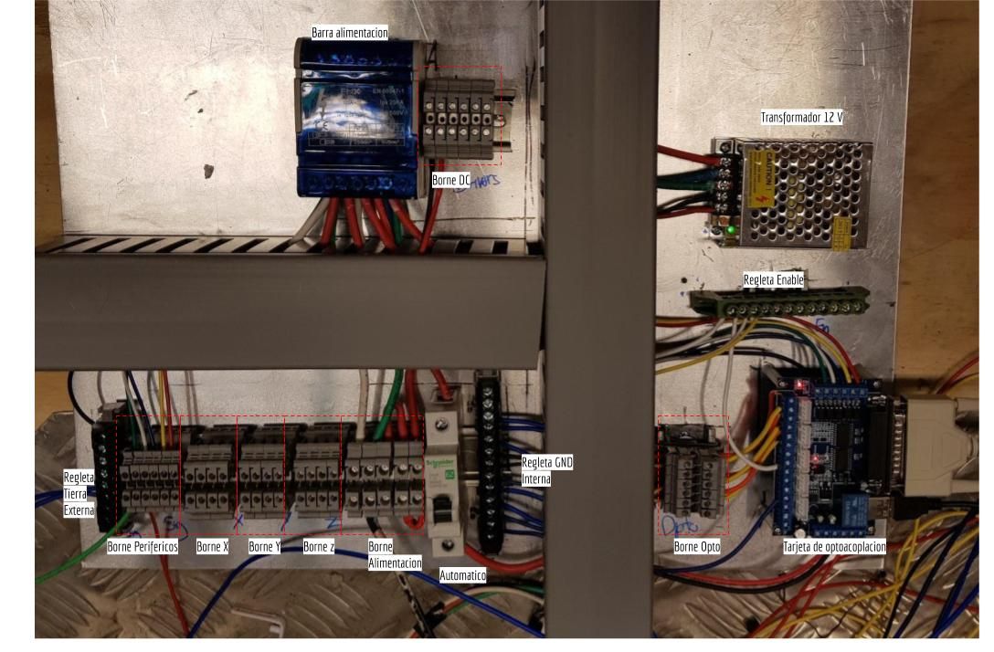
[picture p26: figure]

Implementación lograda de placa de montaje

## Problemas

Como se ha mencionado a lo largo del informe, no se contaron con los componentes comprados para la máquina, no teniendo información precisa de su localización, lo cual dificulto el diseño del tablero y la realización de pruebas. Tampoco se contó con la documentación del trabajo realizado durante el curso de Introducción al Taller de Diseño, por lo cual también se tuvo que hacer esa parte del proyecto. Otra dificultad fue la no posible adquisición del rack y el computador para el plasma CNC, por lo que no se pudo realizar la instalación definitiva de los componentes en la máquina, ni ver el tema del cableado fuera del tablero.

## Conclusiones

Fue posible implementar todo de buena manera. Sin embargo debido a que no hubo comunicación con el equipo mecánico a cargo no fue posible terminar lo pedido en la CNC plasma.

Debido a que al momento de diseñar el tablero ni siquiera se contaba con el modelo de los componentes comprados, no se calcularon bien las dimensiones. Debido a esto es posible que se requiera un segundo tablero o soporte para montar los transformadores. De ser requerido se recomienda agregar bornes externos en el tablero para las entradas y salidas de las fuentes, para mejorar la independencia y movilidad de las piezas.

El trabajo que queda por realizar es:
➔ Reemplazar los cables de alimentación por un menor calibre.
➔ Reemplazar la alimentación de 5 volts por entrada USB por una fuente de alimentación, no requiriendo la conexión USB con el computador.
➔ En caso de que no se pueden encajar todos los elementos faltantes dentro de la placa, escoger entre:
◆ Cambiar la placa de montaje por una más grande, donde se puedan ajustar todos los elementos.
◆ Crear una segunda placa de montaje donde vayan los elementos que no alcanzaron a ir dentro de la primera placa.
➔ Etiquetar los bornes dentro del tablero.
➔ Repensar la conexión del automático. Quizás cortar la alimentación de todos los componentes no sea lo más adecuado. Mientras se busca que unos componentes dejen de funcionar, tal vez sea conveniente que otros sigan energizados mientras se detienen las operaciones.

## Bibliografía

Datasheet Optoacoplador https://warp9td.com/images/BOB_Vendors/StepperOnline/ST-V2.pdf

Datasheet Driver Motor Stepper DM556: http://www.leadshine.com/UploadFile/Down/DM556m.pdf

Datasheet Motor Stepper Nema 23: https://www.cui.com/product/resource/nema23-amt112s.pdf

Diagramas (Draw.io) https://drive.google.com/file/d/1PObYbBdMJArt1ewgQceDJJ7aVt1Wsrb5/view?usp=sharing

Reporte https://docs.google.com/document/d/1rpmf7kgpkObSp1u81GpgjpI0NyfZ58B2krda52GOvmg/edit

Linux CNC; http://linuxcnc.org/docs/html/gui/axis.html

Stepconf Wizard: http://linuxcnc.org/docs/html/config/stepconf.html

GUI Axis: http://linuxcnc.org/docs/html/gui/axis.html

## Anexos

## Configuración Breakout Board CNC con Optoacoplación de 5 ejes


### Outputs de motores

### Inputs de señales


### Outputs de Señales

## Diagrama de conexiones

Barra F; Barra N; Barra T; Automatico; Trafo X 20V; Trafo Y 20V; Trafo Z 20V; Driver Stepper X; Driver Stepper Y; Driver Stepper Z; Regleta Enable; Regleta 5V/ GND; Optoacoplado; B Stop; B tool; B LimX; B LimY; B LimZ; Regleta tierra interruptores; Interruptor Stop; Interruptor tool; Interruptor LimX; Interruptor LimY; Interruptor LimZ; Borne Externo; Borne Interno; Alimentación AC; Alimentación DC; Señal; BE antorcha plasma; Trafo Opto 12V; Barra repartidora; Bornes DC; Borne X; Borne Y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

En general os colores de las conexiones representan los
colores reales utilizados.

Los nombres de algunos elementos pueden variar entre
diagramas

Borne externo alimentacion

BE Int Out Interruptor
Emergencia

BE Int In

## Diseño de tablero electrico

Optoacoplador 9x7cm; GND; LimZ; LimY; LimX; X Pul; X Dir; Y Dir; Y Pul; Z Pul; Z Dir; A Pul; Enable; A Dir; B Pul; B Dir/R; PWM; Spdl int; Cable Paralelo; BORNERAS EXTERNAS; Fuente 20V eje X 22x11m; V- GNDNac Lac; Fuente 20V eje Z 22x11m; Fuente 20V eje Y 22x11m; eje X 10x3cm (vertical); Dir-; Dir+; Pul-; Pul+; Automatico; Regleta GND; Periféricos; Barra Repartidora; Bornes; Bornes AC; Stepper Eje X; Bornes Stepper Eje Y; Bornes Stepper Eje Z; Bornes Perifericos; Bornes DC; Bornes Opto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

Los colores de las conexiones en general reflejan el color
real de los cables en la version implementada.

Notese que ni los drivers ni las fuentes de 20 volts fueron
fijados en la implementacion final

Driver Motor Stepper

Regleta Polo Común

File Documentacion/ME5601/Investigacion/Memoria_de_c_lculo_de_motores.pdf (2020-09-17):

Are the candcnc.com 620 in-oz motors large enough to drive a 150lb PPLLC HD Gantry?

In order to determine the force required, you need to know the weight of the gantry and the acceleration rate required for good plasma cutting.

The weight of a 6’ gantry with motors and torch can be as high as 150 lbs.
The acceleration rate required for good plasma cutting is 35 in/sec/sec

Force = mass x acceleration

When using English units, force has the units of pound force and mass has the units of pound mass.

Looking at the right hand side of the equation,
150 lbm x 35 in/sec/sec = 5250 lbm x in/sec/sec
Since there is 12 inches per foot, we need to divide by 12
5250 / 12 = 437.5 lbm x ft/sec/sec

The relationship between pound force and pound mass is:

### 1 lbf = 1 lbm X gravity

Gravity is 32.174049 ft/sec/sec
Lbf = 437.5 lbm ft/sec/sec / 32.174049 ft/sec/sec
Force required (lbf) = 13.5979 lbf

This is assuming that the linear bearings are frictionless, which they are not.

Next, we need to know the force generated by the belt reduction units driving the gears on the gear rack.

Information needed:
Stepper motor torque 620 in-oz
Belt reduction ratio 3.5:1
Gear pitch diameter 1” PD
Gear rack pressure angle 20 degree

Since there are 16 ozf per lbf 620 / 16 = 38.75 in-lb torque motor
38.75 in-lb x 3.5 reduction = 135.625 in-lb torque reduction
Since the Gear has a 1” PD, the line of force is 1/2” from the center of the shaft to the gear rack. 135.625 in-lb / .5 in = 271.25 lbf

The pressure angle between the gear and rack now needs to be factored in. Since the pressure angle is 20 degrees, the linear force is 271.25 x cosine 20 = 271.25 x .93969 = 254.89 lbf. If you wanted to know the force pushing the gear away from the rack, it would be 271.25 x sine 20 = 271.25 x .342 = 92.77 lbs. This is why a pivoting bracket and spring is not used on our gantry kits. A spring pressure of 100 lbs would be required at all times to handle the force of accelerating the gantry if 100% of the motor torque was used.

Since the gantry has 2 motors driving the 150lb gantry, the maximum force of the belt reduction units is 254.89 lbf x 2 = 509.78 lbf. Since the required torque is 13.5979 lbf, that leaves us with a safety factor of 509.78 / 13.5979 = 37.49 x what is required.

Even when factoring in bearing resistance and gearing / belt reduction efficiency, the motors are many times more powerful than required. That is why the stepper motors work very well in the application and do not lose steps.

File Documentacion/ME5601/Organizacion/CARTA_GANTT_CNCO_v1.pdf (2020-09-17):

Cubicación preliminar del presupuesto; Diseño de piezas en CAD; Simulaciones de resistencia; Rediseño; Compras para estructura de la mesa; Construcción estructura de la mesa; Compras para piscina; Construcción piscina; Diseño sistema de reducción; Diseño cremallera; Solicitud de corte Láser; Compras Sistemas Móviles; Compras Sistemas de Fijación; Ensamblaje cremallera; Ensamblaje eje X; Ensamblaje eje Y; Ensamblaje eje Z; Ensamblaje Portal; Compras componentes eléctricos; Instalación componentes Eléctricos; Ensamblaje sistema de reducción; Pruebas del equipo; Carta Gantt Cortadora Plasma

27-09-2018 07-10-2018 17-10-2018 27-10-2018 06-11-2018 16-11-2018 26-11-2018 06-12-2018 16-12-2018

Diseño sistema de sujeción de cortador plasma


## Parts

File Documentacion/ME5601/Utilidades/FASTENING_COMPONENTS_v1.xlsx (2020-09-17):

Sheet: FASTENING COMPONENTS
FASTENING COMPONENTS
CAR REDUCTION
THREAD SIZE | TYPE | THREAD LENGTH | QTY.
5/16" - 18 | PERNO CABEZA HEXAGONAL | 2" | 6
5/16" - 18 | TUERCA HEXAGONAL | 17/64" | 6
5/16" | GOLILLA PLANA | - | 12
5/16" - 18 | SEPARADOR ROSCADO HEMBRA | 11/8 " | 6
SIDE REDUCTION
THREAD SIZE | TYPE | THREAD LENGTH | QTY.
5/16" - 18 | PERNO CABEZA HEXAGONAL | 2" | 6
5/16" - 18 | TUERCA HEXAGONAL | 17/64" | 6
5/16" | GOLILLA PLANA | - | 12
5/16" - 18 | SEPARADOR ROSCADO HEMBRA | 11/8 " | 6
3/8" - 16 | PERNO CABEZA HEXAGONAL | 7/8" | 7
3/8" | GOLILLA PLANA | - | 8
3/8" - 16 | TUERCA HEXAGONAL | 7/32" | 4
NO. 10 - 32 | PERNO ALLEN | 5/8" | 4
NO. 10 | GOLILLA PLANA | - | 4
NO. 10 - 32 | TUERCA HEXAGONAL | - | 4
GANTRY SUPPORT
THREAD SIZE | TYPE | THREAD LENGTH | QTY.
M12 | TUERCA HEXAGONAL | 6 mm | 4
M12 | PERNO CABEZA HEXAGONAL | 11/8" - 11/4" | 4
M12 | GOLILLA PLANA | - | 4
M12 | TUERCA HEXAGONAL C/FLANGE | - | 2
M12 | TUERCA HEXAGONAL | 10 mm | 2
5/16" - 18 | PERNO CABEZA HEXAGONAL | 1" | 4
5/16" | GOLILLA PLANA | - | 4
5/16" - 18 | TUERCA HEXAGONAL | 3/16" O MENOR | 4
NOTE 1: | EL "THREAD LENGTH" SÓLO ES PARA LOS PERNOS, EN LAS TUERCAS HACE REFERENCIA A LA ALTURA DE ÉSTE.
NOTE 2: | PARA LAS FIJACIONES CON HILO MÉTRICO, COMPRAR LA LONGITUD DEL HILO QUE MÁS SE APROXIME A LA MEDIDA EN PULGADAS.

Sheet: BEARINGS
BEARINGS
GANTRY SUPPORT
TYPE | SUPPLIER | MODEL | QTY.
RODAMIENTO RÍGIDO DE BOLA | SKF | 6001 - Z | 8
DIMENSIONS | D_INT | D_EXT | WIDTH
 | 28 mm | 12 mm | 8 mm

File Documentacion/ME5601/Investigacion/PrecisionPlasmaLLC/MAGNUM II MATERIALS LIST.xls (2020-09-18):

MAGNUM II MATERIALS LIST
QTY | MATERIAL | DESCRIPTION | ALL | 4' WIDE | 5' WIDE | 6' WIDE | 4' LONG | 5' LONG | 8' LONG | 10' LONG
 | LOWER FRAME
2 | 1.5 X 2 X 11 GA WALL RECT TUBE | 1.5X2 TOP TUBES UNDER RAILS |  |  |  |  | 72.00 | 84.00 | 120.00 | 144.00
2 | 3 X 3 X 14 GA TO 1/8 WALL SQ TUBE | 3X3 TOP TUBES UNDER RAILS |  |  |  |  | 72.00 | 84.00 | 120.00 | 144.00
6 | 3 X 3 X 14 GA TO 1/8 WALL SQ TUBE | 3X3 CROSS SUPPORT TUBES |  | 62.00 | 74.00 | 86.00
2 | 3 X 3 X 14 GA TO 1/8 WALL SQ TUBE | 3X3 BOTTOM TUBES |  |  |  |  | 48.00 | 60.00 | 96.00 | 120.00
4 | 3 X 3 X 14 GA TO 1/8 WALL SQ TUBE | 3X3 LEGS | 30.00
2 | 3 X 3 X 14 GA TO 1/8 WALL SQ TUBE | 3X3 CENTER UPRIGHT | 15.00
4 | 1/2 X 3 HOT ROLLED STEEL | FOOT | 4.50
4 | 1/4 X 3 HOT ROLLED STEEL | RAIL END STOPS | 6.50
 | WATERBED
2 | 3 X 3 ANGLE ANY THICKNESS | SIDE ANGLES (MITER ENDS) |  |  |  |  | 54.00 | 66.00 | 102.00 | 126.00
2 | 3 X 3 ANGLE ANY THICKNESS | END ANGLES (MITER ENDS) |  | 54.00 | 66.00 | 78.00
3 | 1 X 2 RECT TUBING ANY THICKNESS | SLAT SUPPORT TUBES |  |  |  |  | 53.50 | 65.50 | 101.50 | 125.50
 | 1 X 1 X ANGLE ANY THICKNESS | SLAT SUPPORT ANGLES | 2.81 |  | QUANTITY REQUIRED |  | 53 | 65 | 101 | 125
1 | 16 GA OR HEAVIER STEEL SHEET | WATERBED BOTTOM | DIMS | 48.00 | 60.00 | 72.00 | 48.00 | 60.00 | 96.00 | 120.00
 | CABLE TRACK SUPPORT
1 | C4 X 4.5 LB/FT STEEL CHANNEL | SUPPORT CHANNEL |  |  |  |  | 66.00 | 78.00 | 66.00 | 78.00
1A | C5 X 6.6 LB/FT STEEL CHANNEL | OPTIONAL SUPPORT CHANNEL FOR OVERSIZED CABLE TRACK |  |  |  |  | 66.00 | 78.00 | 66.00 | 78.00
 | SIDE RAILS
2 | 1/2 X 3 COLD ROLLED STEEL | SIDE RAILS |  |  |  |  | 72.00 | 84.00 | 120.00 | 144.00
 | SLATS |  |  | NOMINAL - MEASURE BED |  |  |  | QUANTITY REQUIRED
 | 1/8 X 2 HOT ROLLED STEEL | SLATS (MEASURE BED) |  | 53.50 | 65.50 | 77.50 | 17 | 21 | 33 | 41
 | GANTRY
1 | 3 X 3 X 14 GA TO 1/8 WALL SQ TUBE | GANTRY MAIN TUBE |  | 69.75 | 81.75 | 93.75
1 | 1 X 3 X 16 GA TO 1/8 RECT TUBE | CABLE TRACK SUPPORT |  | 61.50 | 73.50 | 85.50
2 | C4 OR C5 CHANNEL | SIDE GUSSETS | 3.625

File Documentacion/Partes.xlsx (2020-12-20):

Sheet: mecanica
Item | Cantidad | Costo unidad | Costo total | Comprado? | Ubicación | LINK
Soporte reductora X (SIDE REDUCTION) | 2 |  | 0 | si | corte laser sinsay
Soporte reductora Y (SIDE REDUCTION) | 1 |  | 0 | si | corte laser sinsay
Soporte reductora Z | 1 |  | 0 | si | corte laser sinsay
Barra rectangular para cremallera X | 2 |  |  | si | Otero/Maquimetal
Barra rectangular para cremallera Y | 1 |  | 0 | no | Otero/Maquimetal
Cremallera eje X | 2 |  | 0 | si | Otero/Maquimetal
Cremallera eje Y | 1 |  | 0 | no | Taller Molina
Normalizado cremallera | 1 |  | 0 | no | externo
Barra duraluminio 75mm L150 polea grande | 1 | 10000 | 10000 | no | Otero
Barra duraluminio 25mm L100 polea chica | 1 | 5000 | 5000 | no | Otero
Polea grande XL | 3 | 0 | 0 | no | FabLab | https://www.mcmaster.com/6495K732/
Polea chica XL | 3 | 0 | 0 | no | FabLab | https://www.mcmaster.com/6495K714/
Correa cerrada 136XL | 5 | 3000 | 15000 | si | AliExpress | https://www.aliexpress.com/item/32850771769.html?spm=a2g0o.detail.1000023.10.5a022a99dyNeHv
Ballscrew SFU1605 250mm eje Z | 1 | 45000 | 45000 | si | AliExpress | https://es.aliexpress.com/item/32651221354.html
ruedas para v-slot | 4 | 2500 | 10000 | si | Cimech 3D | https://www.cimech3d.cl/producto/kit-rueda-delrin-rodamientos-para-perfiles-v-slot/
Torcha | 1 | 60000 | 60000 | no | AliExpress | https://www.aliexpress.com/item/4001196665112.html
 |  |  |  |  |  | https://es.aliexpress.com/item/32675566676.html
rodamiento | 16 |  | 0 | si | Vergara
Perno |  |  | 0 |  | Pernos Alameda/KIM
 |  |  | 145000

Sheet: electronica
Item | Cantidad | Costo unidad | Costo total | Comprado? | Proveedor | LINK
Motor Stepper NEMA23 | 4 | 58000 | 232000 | si | Cimech 3D | https://www.cimech3d.cl/producto/motor-stepper-bipolar-nema-23-3-0n-m-2/
Driver stepper NEMA 23 | 4 | 38000 | 152000 | si | Cimech 3D | https://www.cimech3d.cl/producto/dm556-driver-motor-paso-a-paso-5-6a-con-caja-de-proteccion/
Fuente de poder 24V 480W | 4 | 32000 | 128000 | si | Afel | https://afel.cl/producto/fuente-de-poder-24v-20a-480w/
Fuente de poder 12V | 1 | 9000 | 9000 | si | Afel | https://afel.cl/producto/fuente-de-poder-12v-5a-60w/
Optoacoplador | 1 | 10000 | 10000 | si | Cimech 3D | https://www.cimech3d.cl/producto/controlador-puerto-paralelo-para-maquina-de-hasta-5-ejes-sin-cable-paralelo/
Final de carrera | 3 | 3790 | 11370 | si | Cimech 3D | https://www.cimech3d.cl/producto/sensor-inductivo-lj12a3-4-z-bx-deteccion-4mm/
INPUT 220V- input fuentes | metros | subtotal= | 9040
Cable AWG 14 triple | 5 | 950 | 4750 | si | Hobby
Cable AWG 14 BLANCO | 4 | 300 | 1200 | si | Hobby
Cable AWG 14 NEGRO | 4 | 300 | 1200 | si | Hobby
Cable AWG 14 NARANJO | 4 | 300 | 1200 | si | Hobby
Regleta input fuentes AWG 14 | 1 | 690 | 690 | si | Hobby
OUTPUT FUENTES |  | subtotal= | 7500
Cable AWG 10 ROJO | 5 | 750 | 3750 | si | Hobby
Cable AWG 10 NEGRO | 5 | 750 | 3750 | si | Hobby
OUTPUT DRIVERS |  | subtotal= | 60000
Cable AWG 10 ROJO | 20 | 750 | 15000 | si | Hobby
Cable AWG 10 NEGRO | 20 | 750 | 15000 | si | Hobby
Cable AWG 10 VERDE | 20 | 750 | 15000 | si | Hobby
Cable AWG 10 AZUL | 20 | 750 | 15000 | si | Hobby
SEÑALES |  | subtotal= | 14000
Cable AWG 18 ROJO | 25 | 200 | 5000 | si | Hobby | ROLLO 25m
Cable AWG 18 NEGRO | 25 | 200 | 5000 | si | Hobby | ROLLO 25m
Cable AWG 18 CAFE | 10 | 200 | 2000 | si | Hobby
Cable AWG 18 VERDE | 10 | 200 | 2000 | si | Hobby
Regleta señales | 3 | 690 | 2070 | si | Hobby
EXTRAS |  | subtotal= | 41980
gabinete electrico | 1 | 40000 | 40000 | no
Boton emergencia | 1 | 1980 | 1980 | si | Hobby

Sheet: compras1
Item | Cantidad | Costo unidad | Costo total | Comprado? | Proveedor | LINK
Motor Stepper NEMA23 | 1 | 58000 | 58000 | si | Cimech 3D | https://www.cimech3d.cl/producto/motor-stepper-bipolar-nema-23-3-0n-m-2/
Driver stepper NEMA 23 | 2 | 38000 | 76000 | si | Cimech 3D | https://www.cimech3d.cl/producto/dm556-driver-motor-paso-a-paso-5-6a-con-caja-de-proteccion/
Fuente de poder 24V 480W | 4 | 32000 | 128000 | si | Afel | https://afel.cl/producto/fuente-de-poder-24v-20a-480w/
Fuente de poder 12V | 1 | 9000 | 9000 | si | Afel | https://afel.cl/producto/fuente-de-poder-12v-5a-60w/
Final de carrera inductivo | 3 | 3790 | 11370 | si | Cimech 3D | https://www.cimech3d.cl/producto/sensor-inductivo-lj12a3-4-z-bx-deteccion-4mm/
Ballscrew SFU1605 250mm eje Z | 1 | 45000 | 45000 | si | AliExpress | https://es.aliexpress.com/item/32651221354.html
Correa cerrada 136XL | 5 | 3000 | 15000 | si | AliExpress | https://www.aliexpress.com/item/32850771769.html?spm=a2g0o.detail.1000023.10.5a022a99dyNeHv
Optoacoplador | 1 | 10000 | 10000 | si | Cimech 3D | https://www.cimech3d.cl/producto/controlador-puerto-paralelo-para-maquina-de-hasta-5-ejes-sin-cable-paralelo/
 |  | PAGADO | 352370

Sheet: compras2
Item | Cantidad | Costo unidad | Costo total | Comprado? | Proveedor | LINK
INPUT 220V- input fuentes | metros | subtotal= | 9040
Cable AWG 14 triple | 5 | 950 | 4750 | si | Hobby
Cable AWG 14 BLANCO | 4 | 300 | 1200 | si | Hobby
Cable AWG 14 NEGRO | 4 | 300 | 1200 | si | Hobby
Cable AWG 14 NARANJO | 4 | 300 | 1200 | si | Hobby
Regleta input fuentes AWG 14 | 1 | 690 | 690 | si | Hobby
OUTPUT FUENTES |  | subtotal= | 7500
Cable AWG 10 ROJO | 5 | 750 | 3750 | si | Hobby
Cable AWG 10 NEGRO | 5 | 750 | 3750 | si | Hobby
OUTPUT DRIVERS |  | subtotal= | 60000
Cable AWG 10 ROJO | 20 | 750 | 15000 | si | Hobby
Cable AWG 10 NEGRO | 20 | 750 | 15000 | si | Hobby
Cable AWG 10 VERDE | 20 | 750 | 15000 | si | Hobby
Cable AWG 10 AZUL | 20 | 750 | 15000 | si | Hobby
SEÑALES |  | subtotal= | 14000
Cable AWG 18 ROJO | 25 | 200 | 5000 | si | Hobby
Cable AWG 18 NEGRO | 25 | 200 | 5000 | si | Hobby
Cable AWG 18 CAFE | 10 | 200 | 2000 | si | Hobby
Cable AWG 18 VERDE | 10 | 200 | 2000 | si | Hobby
Regleta señales | 3 | 690 | 2070 | si | Hobby
EXTRAS |  | subtotal= | 1980
gabinete electrico | 1 | 40000 | 40000 | no | Hobby
Boton emergencia | 1 | 1980 | 1980 | si | Hobby
MECANICA |  | subtotal=
Barra duraluminio 75mm L150 polea grande | 1 | 10000 | 10000 | no | Otero
Barra duraluminio 25mm L100 polea chica | 1 | 5000 | 5000 | no | Otero
 |  | PAGADO | 94590

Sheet: compras3
Item | Cantidad | Costo unidad | Costo total | Comprado? | Proveedor
OUTPUT DRIVERS |  | subtotal= | 30000
Cable AWG 10 ROJO | 10 | 750 | 7500 | no | Hobby
Cable AWG 10 NEGRO | 10 | 750 | 7500 | no | Hobby
Cable AWG 10 VERDE | 10 | 750 | 7500 | no | Hobby
Cable AWG 10 AZUL | 10 | 750 | 7500 | no | Hobby
Cubre cables (esa cosa que se enrolla) | 10 |  |  | no | Hobby
MECANICA |  | subtotal= | 15000
Barra duraluminio 75mm L150 mm polea grande | 1 | 10000 | 10000 | no | Otero
Barra duraluminio 25mm L100 mm polea chica | 1 | 5000 | 5000 | no | Otero
Placa aluminio 150x200x6 mm | 1 |  |  | no | Maquimetal?
Placa aluminio 320x200x10 mm | 2 |  |  | no | Maquimetal?

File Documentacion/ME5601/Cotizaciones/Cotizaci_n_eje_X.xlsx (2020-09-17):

Ítem | Descripción | Cantidad Q | Unidad | Material precio unitario | Costo material | Equipos/transporte | Subtotal | Comentarios
2.- Eje X: |  |  |  |  |  |  | $86170
2.1 | riel lineal 1500 mm | 1 | unidad | 71280 | 71280 | envio gratis | 71280 | https://amzn.to/2JCAFrX (https://www.youtube.com/redirect?q=https%3A%2F%2Famzn.to%2F2JCAFrX&event=video_description&v=FZbL3MkP7nk)
2.2 | Perfil tubular acero | 4 | metro | 1240 | 7430 | Auto? | 7430 | La tira es de 6m y pesa 10kg
2.3 | soldadura tig | 10 | unidad | 682 | 6820 | 640 | 7460 | Envio desde CN, depende cuanto demore porque este material se necesita para sueldar la cnc
2.4 | soporte para motor | 40x40 | mm |  |  |  | 0 | Se fabrica con la plancha cotizanda por diego landabur
2.5 | Motor steper |  |  |  |  |  | 0 | Incluidos en cotización de cristian
2.6 | cadena (timing pulling) |  |  |  |  |  | 0 | Incluidos en cotización de cristian

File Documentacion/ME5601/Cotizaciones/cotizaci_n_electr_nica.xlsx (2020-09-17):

Ítem | Descripción | Cantidad Q | Unidad | Material precio unitario | Costo material | Equipos/transporte | Subtotal | Comentarios
5. Componentes electrónicos |  |  |  |  |  |  | $466842.00
5.1 | Nema 23 425 oz in Stepper Motor 4.2A | 3 | unid. | $51990.00 | $155970.00 | $3264.00 | $159234.00 | De acuerdo a los foros que econtré, este tipo de CNC no requieren muhco TQ en sus motores (a diferencia de una CNC mill), estando entre 300 y 600 oz in. https://articulo.mercadolibre.cl/MLC-464435120-nema-23-stepper-motor-42a-30nm-425ozin-100-mm-de-_JM
5.2 | Controlador Stepper Motor TB6600 12-48V @ 2-5A | 3 | unid. | $19000.00 | $57000.00 | $0.00 | $57000.00 | Fuente: https://afel.cl/producto/driver-motor-paso-a-paso-tb6600-0-2-5a-12-48vdc/
5.3 | Fuente de Poder Stepper Motor 100W 24V @ 4.5A | 3 | unid. | $37990.00 | $113970.00 | $3264.00 | $117234.00 | Idealmente, debiese ser de 36V @ 5A. Pero no pude encontrar uno en Chile. Fuente: https://articulo.mercadolibre.cl/MLC-464435467-fuente-de-alimentacion-conmutada-100w-24v-45a-para-_JM
5.4 | Módulo Relé de 4 Canales | 3 | unid. | $4500.00 | $13500.00 | $3698.00 | $17198.00 | Fuente: https://articulo.mercadolibre.cl/MLC-451582465-modulo-rele-4-canales-arduino-raspberry-microcontrolador-_JM
5.5 | Sensores de Proximidad | 2 | unid. | $11500.00 | $23000.00 | $0.00 | $23000.00 | Fuente: https://articulo.mercadolibre.cl/MLC-460437255-sensor-proximidad-capacitivo-para-cnc-detector-scontacto-_JM
5.6 | Cables Extensión 18AWG 5C | 1 | 40 pies | $46000.00 | $46000.00 | $0.00 | $46000.00 | Fuente: https://articulo.mercadolibre.cl/MLC-461480308-rgbsight-40ft-18-calibre-rgbw-led-tira-de-extension-cable-_JM
5.7 | Cadena de Manejo de Cables | 4 | metros | $9144.00 | $36576.00 | $0.00 | $36576.00 | Puede convenir comprar de China (Envío gratis). https://www.ebay.com/itm/15-x-30mm-1M-Plastic-Drag-Chain-40-Towline-Carrier-Wire-Cable-CNC-Machine-Tool/272976655754
5.8 | Paradas de Emergencia | 2 | unid. | $5300.00 | $10600.00 | $0.00 | $10600.00 | Fuente: http://www.victronics.cl/

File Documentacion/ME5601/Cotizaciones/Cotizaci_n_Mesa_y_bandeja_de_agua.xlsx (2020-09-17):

Ítem | Descripción | Cantidad Q | Unidad | Material precio unitario | Costo material | Equipos/transporte | Subtotal | Comentarios
1.- Mesa y bandeja de agua |  |  |  |  |  |  | $74190
1.1 | perfil rectangular acero génerico 6 metros 40x40x2 mm | 5 | tiras | 10460 |  |  | 52300 | Sodimac
1.1 | perfil rectangular acero génerico 6 metros 15x15x2.5 mm | 1 | tiras | 2190 |  |  | 2190 | Sodimac
1.3 | perfil ángulo doblado 6 metros 40x40x2 | 1 | tiras | 5500 |  |  | 5500 | Marca VH (Sodimac)
1.4 | plancha acero inoxidable 2.5x2.5 | 1 | unidad | 14200 |  |  | 14200 | No se encontró las dimensiones requeridas, de momento se utiliza el precio de referencia cotizado por diego landabur
1.5 | Pletinas acero inoxidable 2.5mx10cmx5mm | 40 | unidad | ? |  |  |  | No se encontró precios por unidad de largo, por lo que se requiere cotizar directamente con algún proveedor

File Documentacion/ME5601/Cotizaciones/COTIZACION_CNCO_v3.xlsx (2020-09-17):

Ítem | Descripción | Cantidad Q | Unidad | Material precio unitario | Costo material | Equipos/transporte | Subtotal | Comentarios
0. Ensamble Completo |  |  |  |  |  |  | $1004906
1. Mesa y bandeja de agua |  |  |  |  |  |  | $231120
1.1 | Perfil cuadrado acero génerico 6 metros 75x75x3 mm | 6 | tiras | $31480.00 |  |  | $188880 | Fuente: www.sodimac.cl/sodimac-cl/product/165263/75x75-x-3-mm-x-6-mt-Perfil-Tubular-Cuadrado
1.2 | Perfil rectangular 6 metros 60x40x2 | 1 | tiras | $13840.00 |  |  | $13840 | Fuente: www.easy.cl/es/easy-chile/fierro/perfiles-de-fierro/perfiles-cerrados/perfil-rectangulo-60-x-40-x-2-mm-acero-6-mt-cintac-119322p
1.4 | Plancha Acero Laminado en frio 0.8x1000x3000 mm | 2 | unidad | $14200.00 |  |  | $28400 | No se encontró precios por unidad de largo, por lo que se requiere cotizar directamente con algún proveedor, se puede considerar cortar una plancha de acero al carbono.
2. Eje X: |  |  |  |  |  |  | $14890
2.2 | Perfil tubular acero | 4 | metro | $1240.00 | $7430.00 | Auto? | $7430 | La tira es de 6m y pesa 10kg
2.3 | Soldadura tig | 10 | unidad | $682.00 | $6820.00 | $640.00 | $7460 | Envio desde CN, depende cuanto demore porque este material se necesita para sueldar la cnc
3. Eje Y: |  |  |  |  |  |  | $99458
3.2 | Rodamiento lineal de movimiento horizontal | 2 | un | $21777.00 | $43554.00 |  | $43554 | Transporte incluido.
3.3 | Lámina de acero laminado en caliente 2mmx1mx3m | 1 | un | $36490.00 | $36490.00 |  | $36490 | Se requiere poco material. Uso de dimensiones comerciales. Se pueden encontrar láminas más pequeñas en un proveedor especializado.
3.4 | Perno allen M6 | 16 | un | $200.00 | $3200.00 |  | $3200 | Venta de caja de 50 unidades.
3.5 | Polea | 4 | un | $2521.00 | $10084.00 |  | $10084 | Precio no incluye IVA. Envío gratis.
3.6 | Perno Cabeza Hexagonal 1/4 " | 4 | un | $247.50 | $990.00 |  | $990 | Se vende la caja de 4 unidades.
3.8 | Perfil en L de Acero 20 x 20 x 3 mm x 6 mt | 1 | un | $3750.00 | $3750.00 |  | $3750 | Material Prescindible. Se puede obtener de un perfil cuadrado que sobre, pues se usará una cantidad pequeña.
3.9 | Perno Cabeza Hexagonal 3/8 " | 2 | un | $695.00 | $1390.00 |  | $1390 | Venta de caja de 2 unidades.
4. Eje Z |  |  |  |  |  |  | $74256
4.1 | Plancha Acero Laminado en frio 0.8x1000x3000 mm | 1 | m^3 | $14200.00 | $14200.00 | - | $14200 | Principalmente para recortes, por lo cual si existiera una placa de características similares en el taller podríamos realizar los recortes de ella y prescindir de esta compra
4.2 | Kit Transmision de movimiento (8mm) (400mm largo) | 1 | - | $49990.00 | $49990.00 | - | $49990 | Incluye: Rodamiento lineal x 4, soporte eje 8mm x 4, Soporte de pie rodamiento bola x 2, Acople flexible x 1, Varilla Roscada 8mmx400mm x 1, Eje acero 8mmx400mm x 2
4.4 | Perno Parker ac.inox 5/16 x 1½ NC | 24 | - | $348.00 | $8352.00 | - | $8352
4.5 | Perno Parker ac.inox 3/16 x ½ NC | 4 | - | $81.00 | $324.00 | - | $324
4.6 | Roscalata 10x3" 10 unidades | 1 | - | $1390.00 | $1390.00 | - | $1390
5. Componentes electrónicos |  |  |  |  |  |  | $575822
5.1 | Nema 23 425 oz in Stepper Motor 4.2A | 4 | unid. | $51990.00 | $155970.00 | $3264.00 | $211224 | De acuerdo a los foros que econtré, este tipo de CNC no requieren muhco TQ en sus motores (a diferencia de una CNC mill), estando entre 300 y 600 oz in. https://articulo.mercadolibre.cl/MLC-464435120-nema-23-stepper-motor-42a-30nm-425ozin-100-mm-de-_JM
5.2 | Controlador Stepper Motor TB6600 12-48V @ 2-5A | 4 | unid. | $19000.00 | $57000.00 | $0.00 | $76000 | Fuente: https://afel.cl/producto/driver-motor-paso-a-paso-tb6600-0-2-5a-12-48vdc/
5.3 | Fuente de Poder Stepper Motor 100W 24V @ 4.5A | 4 | unid. | $37990.00 | $113970.00 | $3264.00 | $155224 | Idealmente, debiese ser de 36V @ 5A. Pero no pude encontrar uno en Chile. Fuente: https://articulo.mercadolibre.cl/MLC-464435467-fuente-de-alimentacion-conmutada-100w-24v-45a-para-_JM
5.4 | Módulo Relé de 4 Canales | 3 | unid. | $4500.00 | $13500.00 | $3698.00 | $17198 | Fuente: https://articulo.mercadolibre.cl/MLC-451582465-modulo-rele-4-canales-arduino-raspberry-microcontrolador-_JM
5.5 | Sensores de Proximidad | 2 | unid. | $11500.00 | $23000.00 | $0.00 | $23000 | Fuente: https://articulo.mercadolibre.cl/MLC-460437255-sensor-proximidad-capacitivo-para-cnc-detector-scontacto-_JM
5.6 | Cables Extensión 18AWG 5C | 1 | 40 pies | $46000.00 | $46000.00 | $0.00 | $46000 | Fuente: https://articulo.mercadolibre.cl/MLC-461480308-rgbsight-40ft-18-calibre-rgbw-led-tira-de-extension-cable-_JM
5.7 | Cadena de Manejo de Cables | 4 | metros | $9144.00 | $36576.00 | $0.00 | $36576 | Puede convenir comprar de China (Envío gratis). https://www.ebay.com/itm/15-x-30mm-1M-Plastic-Drag-Chain-40-Towline-Carrier-Wire-Cable-CNC-Machine-Tool/272976655754
5.8 | Paradas de Emergencia | 2 | unid. | $5300.00 | $10600.00 | $0.00 | $10600 | Fuente: http://www.victronics.cl/
6. Otros |  |  |  |  |  |  | $9360
6.1 | Disco de corte tronzadora Dewalt 14'' | 2 | unid | $4680.00 |  |  | 9360 | Homecenter Sodimac

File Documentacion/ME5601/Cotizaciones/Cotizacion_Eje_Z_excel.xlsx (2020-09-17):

Item | Descripcion | Cantidad | Unidad | Precio Unitario | Costo Material | Equipos/Transporte | Subtotal | Comentarios
1.Eje Z
1.1 | Plancha Laminado en frio 0.8x1000x3000 mm | 1 | m^3 | 14200 | 14200 | 0 | 14200 | Principalmente para recortes, por lo cual si existiera una placa de caracteristicas similares en el taller podriamos realizar los recortes de ella y prescindir de esta compra
1.2 | Kit Transmision de movimiento (8mm) (400mm largo) | 1 | - | 49990 | 49990 | - | 49990 | Incluye: Rodamiento lineal x 4, soporte eje 8mm x 4, Soporte de pie rodamiento bola x 2, Acople flexible x 1, Varilla Roscada 8mmx400mm x 1, Eje acero 8mmx400mm x 2
1.3 | Stepper Motor Nema 23 30 kg-cm | 1 | - | 53681 | 53681 | - | 53681
1.4 | Perno Parker ac.inox 5/16 x 1½ NC | 24 | - | 348 | 8352 | - | 8352
1.5 | Perno Parker ac.inox 3/16 x ½ NC | 4 | - | 81 | 324 | - | 324
1.6 | Roscalata 10x3" 10 unidades | 1 | - | 1390 | 1390 | - | 1390

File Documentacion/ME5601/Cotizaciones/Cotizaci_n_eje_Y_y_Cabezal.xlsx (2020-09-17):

Ítem | Descripción | Cantidad | Unidad | Precio unitario | Costo material | Transporte | Subtotal | Comentarios
1. Sistema Móvil Cabezal en la dirección Y |  |  |  |  |  |  | 447586
2018-01-01 | Riel guía para transporte del rodamiento lineal | 4.4 | m | 79.12 | 348128 |  | 348128 | Transporte incluido. Debido al precio, revisar si existe en Chile u Otra página estadounidense como la usada por Vayron Mac-Lean.
2018-02-01 | Rodamiento lineal de movimiento horizontal | 2 | un | 21777 | 43554 |  | 43554 | Transporte incluido.
2018-03-01 | Lámina de acero laminado en caliente 2mmx1mx3m | 1 | un | 36490 | 36490 |  | 36490 | Se requiere poco material. Uso de dimensiones comerciales. Se pueden encontrar láminas más pequeñas en un proveedor especializado.
2018-04-01 | Perno allen M6 | 16 | un | 200 | 3200 |  | 3200 | Venta de caja de 50 unidades.
2018-05-01 | Polea | 4 | un | 2521 | 10084 |  | 10084 | Precio no incluye IVA. Envío gratis.
2018-06-01 | Perno Cabeza Hexagonal 1/4 " | 4 | un | 247.5 | 990 |  | 990 | Se vende la caja de 4 unidades.
2018-07-01 | Correa dentada | 5 | m |  |  |  |  | Cotización realizada por Cristian Herrera
2018-08-01 | Perfil en L de Acero 20 x 20 x 3 mm x 6 mt | 1 | un | 3750 | 3750 |  | 3750 | Material Prescindible. Se puede obtener de un perfil cuadrado que sobre, pues se usará una cantidad pequeña.
2018-09-01 | Perno Cabeza Hexagonal 3/8 " | 2 | un | 695 | 1390 |  | 1390 | Venta de caja de 2 unidades.
2. Estructura del cabezal |  |  |  |  |  |  | 6950
2018-01-02 | Perfil cuadrado de Acero | 3.5 | m |  |  |  |  | Cotizado por Cristóbal Doña.
2018-02-02 | Lámina de Acero | 4 | un |  |  |  |  | Se usará parte de la lámina cotizada en el subsistema 1.
2018-03-02 | Perno Cabeza Hexagonal 3/8 " | 10 | un | 695 | 6950 |  | 6950

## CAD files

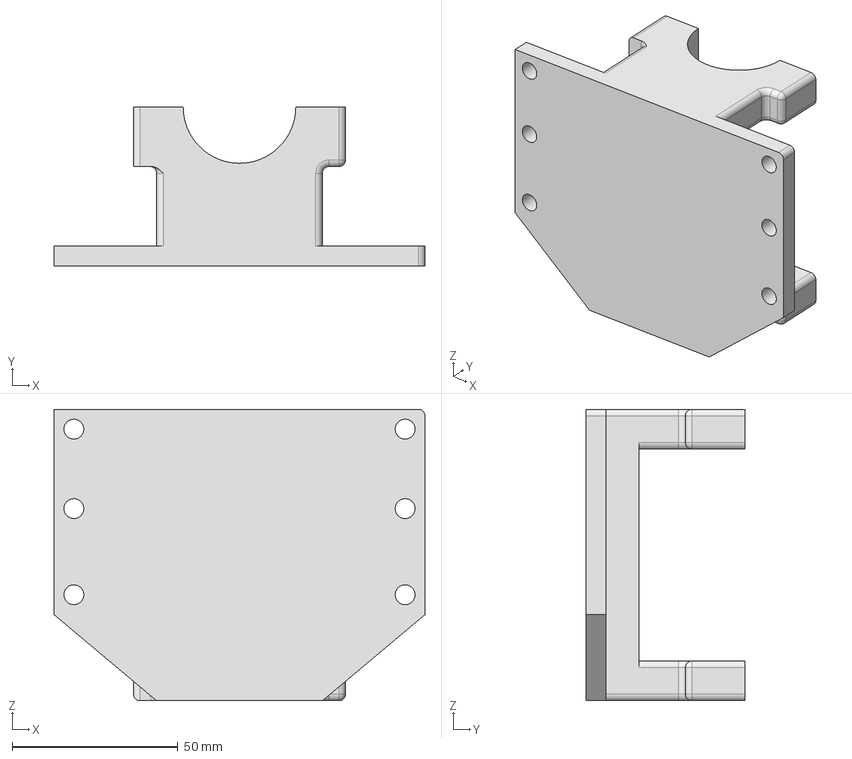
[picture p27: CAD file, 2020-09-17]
Documentacion/ME5601/CADs/CNC_Z_SUPPORT/Soporte.stp
112.0 x 48.0 x 88.0 mm

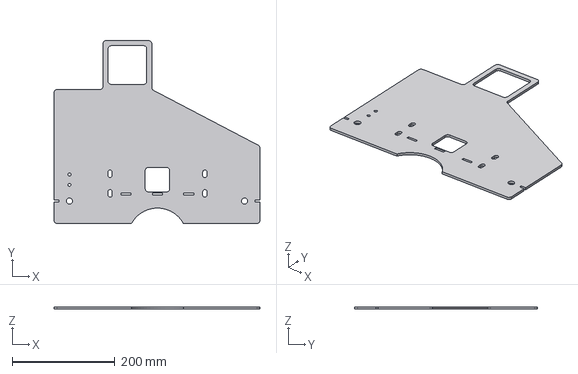
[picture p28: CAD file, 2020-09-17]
Documentacion/ME5601/CADs/CORTES_L_SER_RAIL_SUPPORT/EXTERNAL SIDE PLATE_v2.stp
400.0 x 355.0 x 4.45 mm

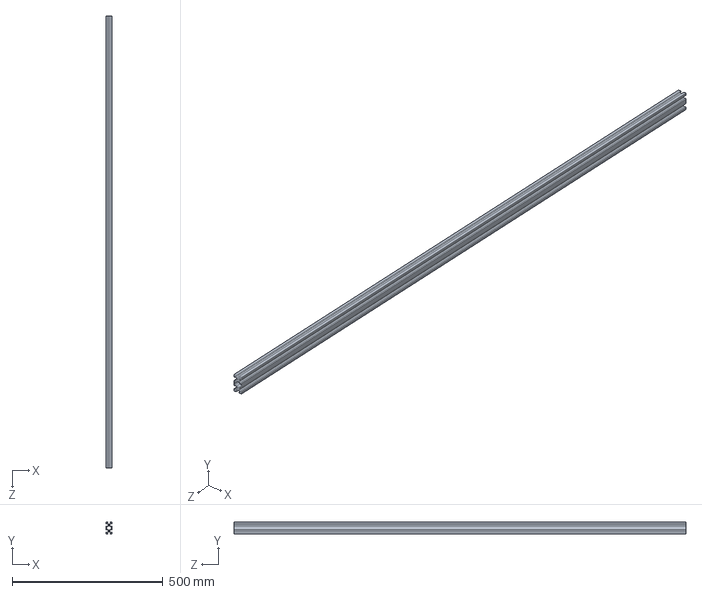
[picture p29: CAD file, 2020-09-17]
Documentacion/ME5601/CADs/Perfil_Aluminio_V_Slot_20x40x1500mm_Cimech_3D_1_/Perfil Aluminio V-Slot 20x40x1500mm Cimech 3D.step
20.0 x 40.0 x 1500.0 mm

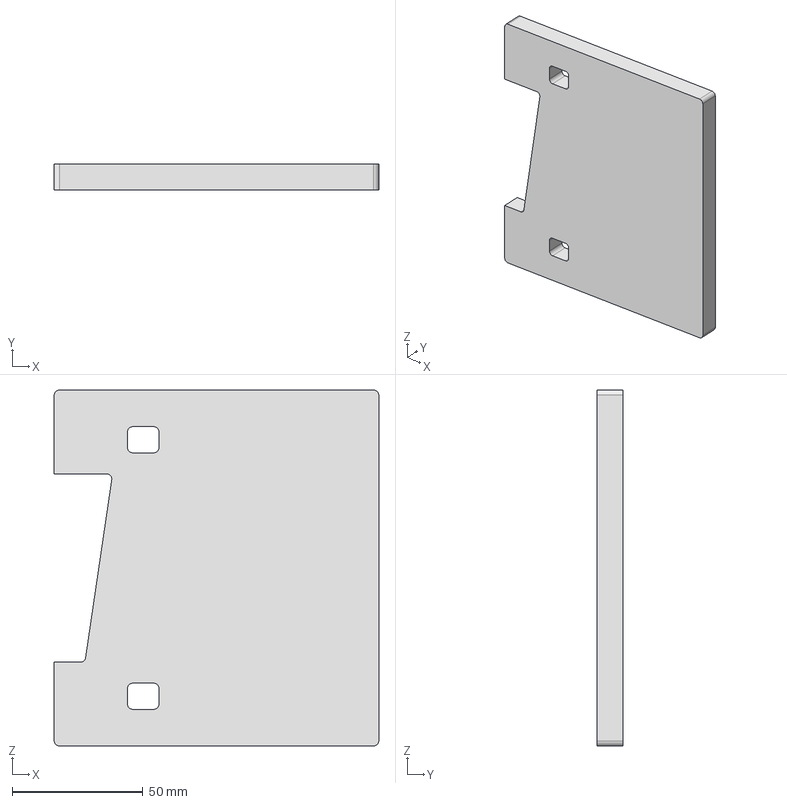
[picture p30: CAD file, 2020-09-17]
Documentacion/ME5601/CADs/CNC_Z_SUPPORT/PlacaSensor.stp
124.0 x 10.0 x 136.0 mm

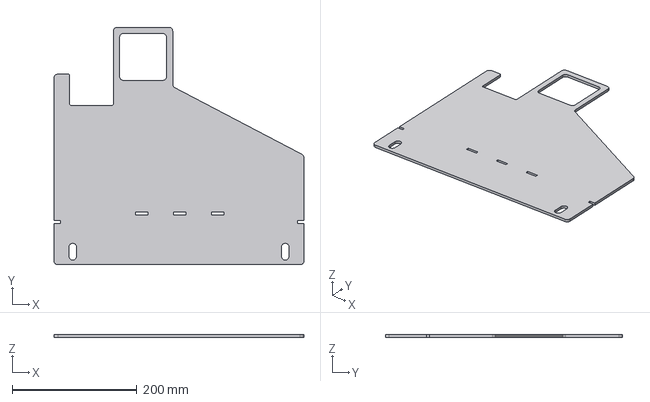
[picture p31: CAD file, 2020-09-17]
Documentacion/ME5601/CADs/CORTES_L_SER_RAIL_SUPPORT/INTERNAL SIDE PLATE_v2.stp
400.0 x 380.0 x 4.45 mm

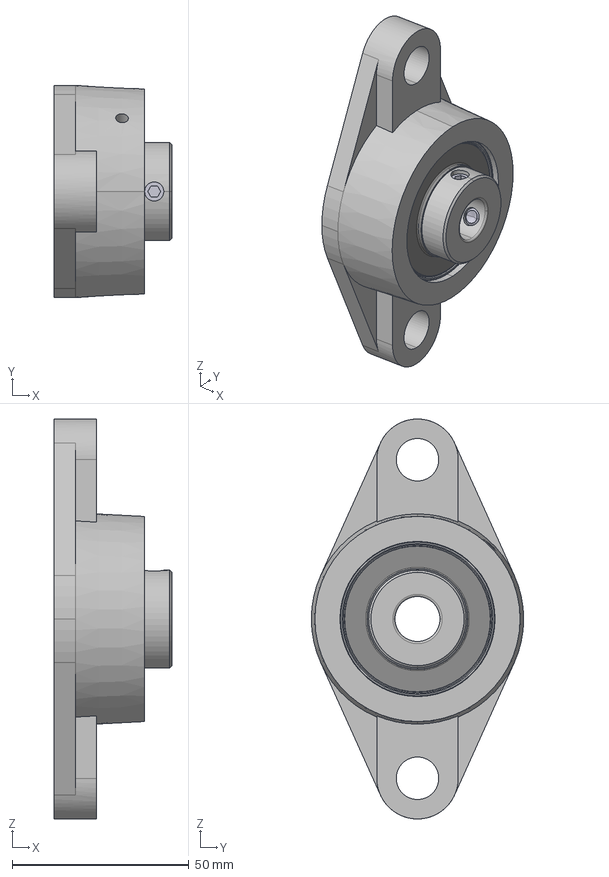
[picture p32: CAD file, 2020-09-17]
Documentacion/ME5601/CADs/CNCO_SIDE_REDUCTION/UCFL201-08 TWO-BOLT FLANGE BEARING/inafag_ucfl201-08_8iwm4vnff3g45oi9d3mfhiexc.stp
33.3 x 60.0 x 113.0 mm

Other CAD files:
Documentacion/ME5601/CADs/CNCO_SIDE_REDUCTION/MAG 7 SIDE RED.dwg
Documentacion/ME5601/CADs/CNCO_GANTRY/Frame/1950 STEEL PROFILE.ipt
Documentacion/ME5601/CADs/CNCO_GANTRY/Frame/2100 STEEL PROFILE.ipt
Documentacion/ME5601/CADs/CNCO_GANTRY/Frame/2570 STEEL PROFILE.ipt
Documentacion/ME5601/CADs/CNCO_GANTRY/Frame/450 STEEL PROFILE.ipt
Documentacion/ME5601/CADs/CNCO_GANTRY/Frame/750 STEEL PROFILE.ipt
Documentacion/ME5601/CADs/CNCO_GANTRY/Frame/OldVersions/1950 STEEL PROFILE.0002.ipt
Documentacion/ME5601/CADs/CNCO_GANTRY/Frame/OldVersions/2100 STEEL PROFILE.0006.ipt
Documentacion/ME5601/CADs/CNCO_GANTRY/Frame/OldVersions/2570 STEEL PROFILE.0003.ipt
Documentacion/ME5601/CADs/CNCO_GANTRY/Frame/OldVersions/450 STEEL PROFILE.0003.ipt
Documentacion/ME5601/CADs/CNCO_GANTRY/Frame/OldVersions/750 STEEL PROFILE.0004.ipt
Documentacion/ME5601/CADs/CNCO_GANTRY/Frame/OldVersions/STEEL FRAME ASSY.0003.iam
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

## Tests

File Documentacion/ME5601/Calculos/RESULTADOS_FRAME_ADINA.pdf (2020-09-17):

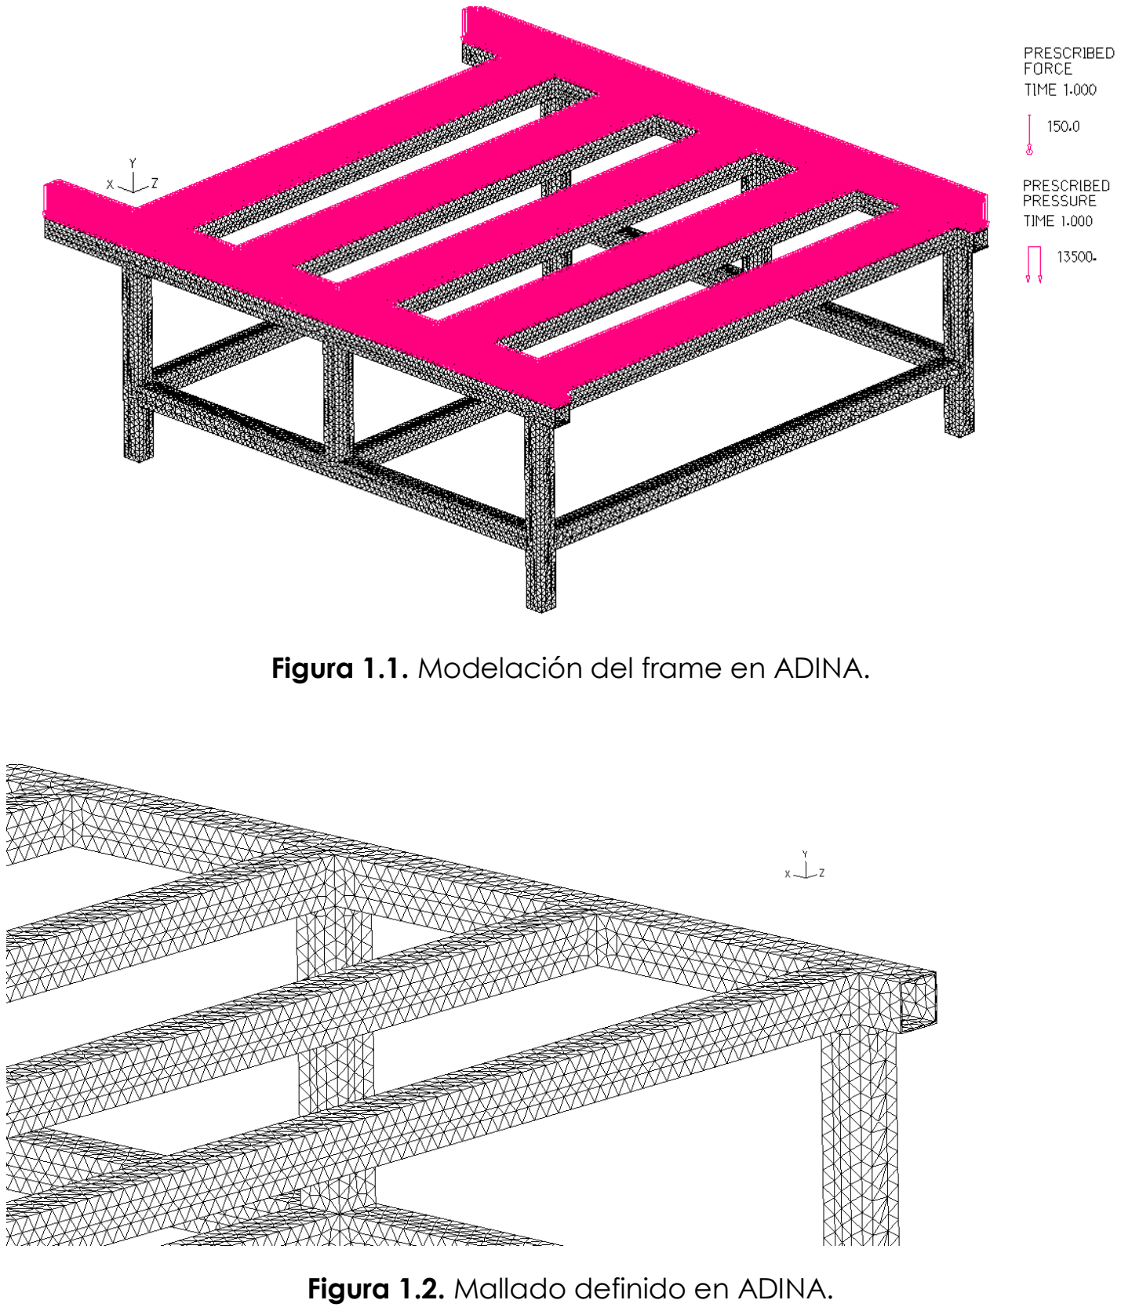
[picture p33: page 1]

Figura 1.1. Modelación del frame en ADINA.

Figura 1.2. Mallado definido en ADINA.

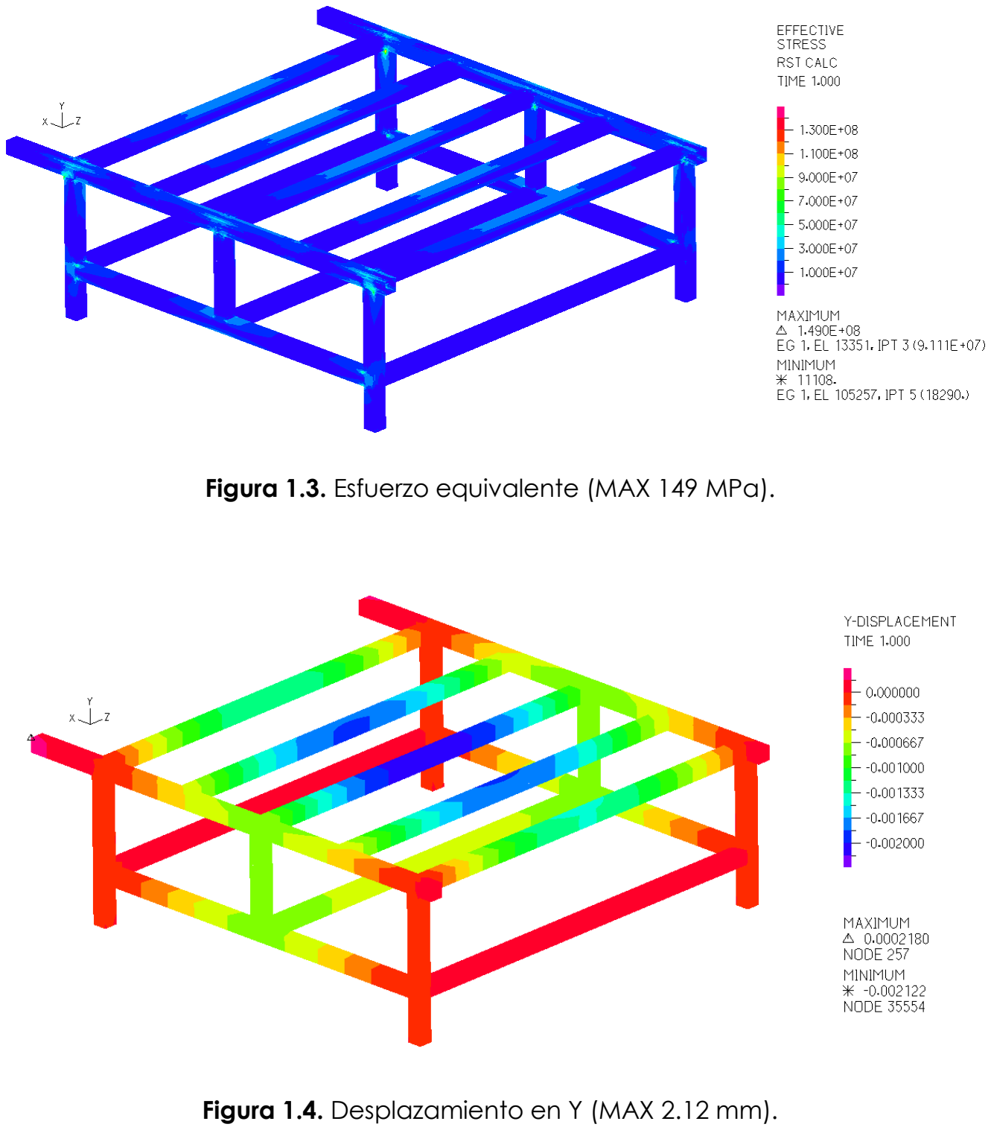
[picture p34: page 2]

Figura 1.3. Esfuerzo equivalente (MAX 149 MPa).

Figura 1.4. Desplazamiento en Y (MAX 2.12 mm).

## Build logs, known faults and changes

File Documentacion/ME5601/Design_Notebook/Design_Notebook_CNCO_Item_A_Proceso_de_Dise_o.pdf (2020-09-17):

### Proceso de diseño

Definición del prototipo
(Descripción ingeniería conceptual anterior, recolección de antecedentes (planos e informes anteriores), identificar brechas existentes entre conceptual, maqueta y problemática real.)

Debido al poco tiempo de construcción y a que no se está implementando un diseño innovador y más bien se está construyendo algo existente, no es necesario definir un prototipo, por lo que se define el modelo definitivo de la mesa CNC Plasma sujeta a cambios.
El diseño está basado principalmente en los planos de ensamble de una mesa ya existente “La Magnum 7 HD”, pero que facilita la construcción, permite asignar más tiempo de trabajo a la construcción ahorrando tiempo en diseño y se eligió este diseño principalmente porque para el movimiento del eje X y del eje Y se utiliza un sistema de engrane-cremallera, lo que aunque dificulta la manufactura, ya que se debe construir en el taller molina, abarata costos evitando el uso de rodamientos lineales, los cuales además de ser costosos, deben ser traídos desde el extranjero, con un tiempo de 2 a 3 meses de demora.
Este modelo consta principalmente de una mesa formada por perfiles de acero para estructuras de 75x75x3mm, los cuales se unen mediante soldadura. Además se tiene una bandeja de agua de acero galvanizado, un portal, un ensamble para el movimiento de los ejes X, Y y Z, en los cuales se contemplan motores tipo stepper y un láser.
Las dimensiones principales de la mesa son un ancho de 2.250 [mm], un largo de 2.570 [mm] y una altura de 825 [mm], estos valores están fijados debido a los requerimientos del cliente.

A continuación se muestran los principales planos de ensamble de la mesa Magnum 7 HD en los cuales se basa el proyecto.

Figura 1 Plano de la mesa

Figura 2 Plano del portal

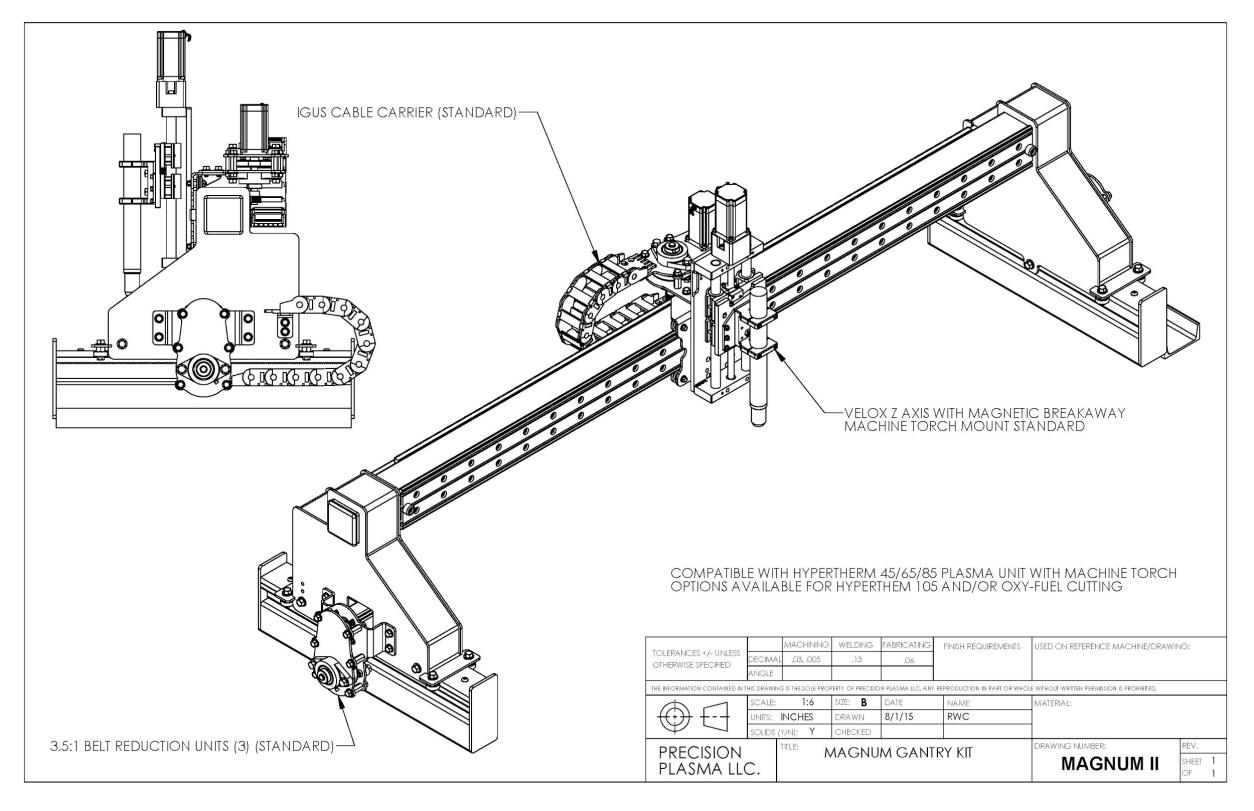
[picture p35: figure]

Figura 3 Plano de la bandeja de agua

Figura 4 Plano de los patines, eje X

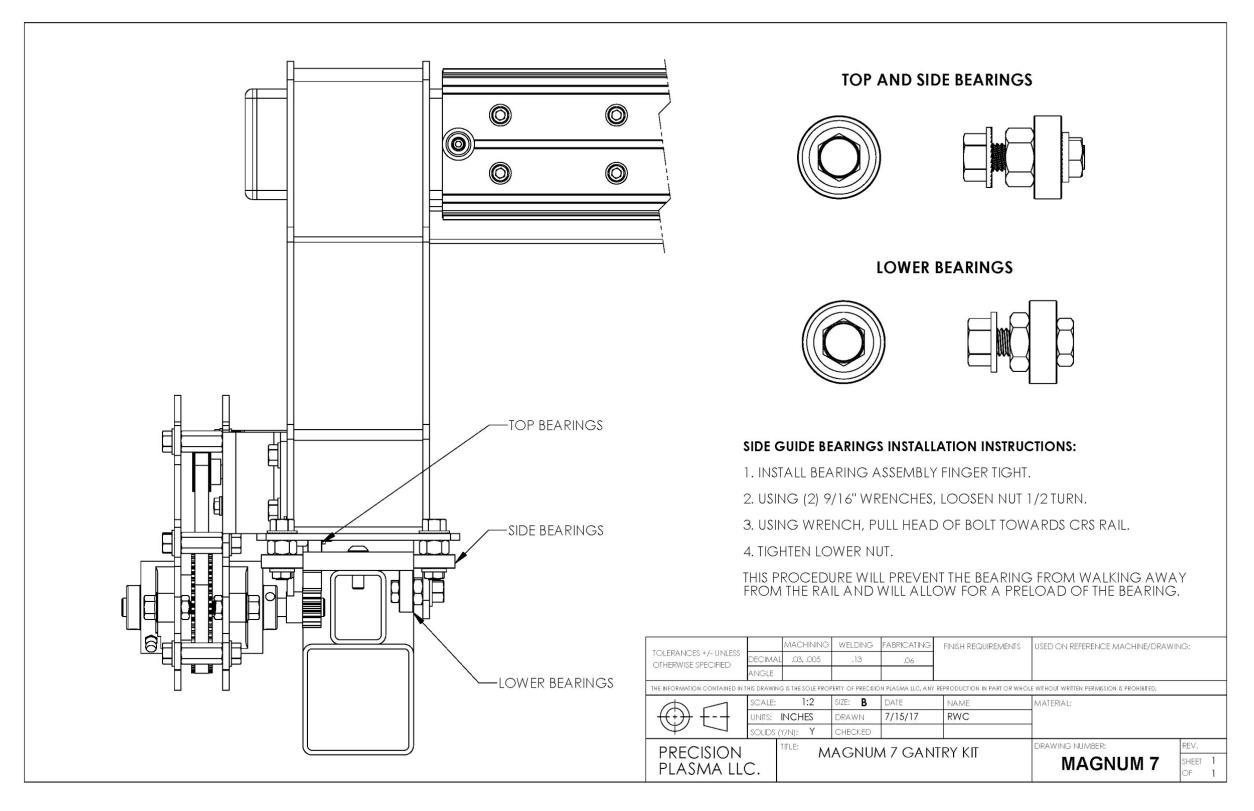
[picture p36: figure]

Figura 5 Plano de ensamble del eje Z

Brechas entre diseño conceptual y realidad

Al diseñar la CNC, hay ciertos aspectos que chocan con la realidad, hasta el momento nos hemos topado con las siguientes dificultades:
-Construcción de la piscina (no basta con solo una placa, se deben soldar dos placas y evitar la fuga de agua, además de soldar en las esquinas)
-Dificultad al construir la cremallera y al elegir el sistema de reducción
-Adaptar el eje z con las especificaciones de la pistola láser en el taller del DIMEC.

Desarrollo de ideas de mejora
(Listado de ventajas y desventajas, gráficos que ayuden a organizar ideas, Fotografías de conceptos, bosquejos, maquetas, esquemas o dibujos a mano, videos o fotos de ideas o soluciones similares que apoyen su proceso de diseño)

Primera idea de diseño de la mesa: https://www.youtube.com/playlist?list=PL4lExYUFHSPy926ACka0Rf6WGTWqWWXS4

En un principio el proyecto se iba a basar en este diseño, pero posteriormente el profesor nos indicó un modelo en el cual se evitaban los rodamientos lineales, ahorrando costos principalmente, además contaba con la ventaja de que era un diseño existente, por lo que a priori no debería tener problemas en su implementación.

Segunda idea de diseño: http://precisionplasmallc.com/My_Homepage_Files/Page3.html

Ventajas y desventajas del diseño magnum 7 HD

Ventajas:
- Tiene planos de ensamble disponibles.
- Uso de cremallera
- Perfiles de acero, baratos en comparación a los de aluminio Desventajas:
- Planos son de distinta medida a la requerida
- Restringe el diseño
- No se puede desensamblar.

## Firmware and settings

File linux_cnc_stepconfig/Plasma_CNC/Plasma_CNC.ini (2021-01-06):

# Generated by stepconf 1.1 at Tue Oct 20 21:39:12 2020
# If you make changes to this file, they will be
# overwritten when you run stepconf again

[EMC]
MACHINE = Plasma_CNC
DEBUG = 0
VERSION = 1.1

[DISPLAY]
DISPLAY = axis
EDITOR = gedit
POSITION_OFFSET = RELATIVE
POSITION_FEEDBACK = ACTUAL
ARCDIVISION = 64
GRIDS = 10mm 20mm 50mm 100mm 1in 2in 5in 10in
MAX_FEED_OVERRIDE = 1.2
MIN_SPINDLE_OVERRIDE = 0.5
MAX_SPINDLE_OVERRIDE = 1.2
DEFAULT_LINEAR_VELOCITY = 3.75
MIN_LINEAR_VELOCITY = 0
MAX_LINEAR_VELOCITY = 37.50
INTRO_GRAPHIC = linuxcnc.gif
INTRO_TIME = 5
PROGRAM_PREFIX = /home/cnc-dimec/linuxcnc/nc_files
INCREMENTS = 5mm 1mm .5mm .1mm .05mm .01mm .005mm

[KINS]
JOINTS = 3
KINEMATICS = trivkins coordinates=XYZ

[FILTER]
PROGRAM_EXTENSION = .png,.gif,.jpg Greyscale Depth Image
PROGRAM_EXTENSION = .py Python Script
PROGRAM_EXTENSION = .nc,.tap G-Code File
png = image-to-gcode
gif = image-to-gcode
jpg = image-to-gcode
py = python

[TASK]
TASK = milltask
CYCLE_TIME = 0.010

[RS274NGC]
PARAMETER_FILE = linuxcnc.var

[EMCMOT]
EMCMOT = motmod
COMM_TIMEOUT = 1.0
BASE_PERIOD = 62500
SERVO_PERIOD = 1000000

[HAL]
HALFILE = Plasma_CNC.hal
HALFILE = custom.hal
POSTGUI_HALFILE = postgui_call_list.hal

[TRAJ]
COORDINATES =  X Y Z
LINEAR_UNITS = mm
ANGULAR_UNITS = degree
DEFAULT_LINEAR_VELOCITY = 3.75
MAX_LINEAR_VELOCITY = 37.50

[EMCIO]
EMCIO = io
CYCLE_TIME = 0.100
TOOL_TABLE = tool.tbl

[AXIS_X]
MAX_VELOCITY = 37.5
MAX_ACCELERATION = 750.0
MIN_LIMIT = -0.001
MAX_LIMIT = 2000.0

[JOINT_0]
TYPE = LINEAR
HOME = 0.0
MIN_LIMIT = -0.001
MAX_LIMIT = 2000.0
MAX_VELOCITY = 37.5
MAX_ACCELERATION = 750.0
STEPGEN_MAXACCEL = 937.5
SCALE = 26.6774024102
FERROR = 1
MIN_FERROR = .25
HOME_OFFSET = 0.000000
HOME_SEARCH_VEL = -5.000000
HOME_LATCH_VEL = -5.000000
HOME_SEQUENCE = 1

[AXIS_Y]
MAX_VELOCITY = 37.5
MAX_ACCELERATION = 750.0
MIN_LIMIT = -0.001
MAX_LIMIT = 2000.0

[JOINT_1]
TYPE = LINEAR
HOME = 0.0
MIN_LIMIT = -0.001
MAX_LIMIT = 2000.0
MAX_VELOCITY = 37.5
MAX_ACCELERATION = 750.0
STEPGEN_MAXACCEL = 937.5
SCALE = 26.6774024102
FERROR = 1
MIN_FERROR = .25
HOME_OFFSET = 0.000000
HOME_SEARCH_VEL = -5.000000
HOME_LATCH_VEL = -5.000000
HOME_SEQUENCE = 2

[AXIS_Z]
MAX_VELOCITY = 23.75
MAX_ACCELERATION = 750.0
MIN_LIMIT = 0.0
MAX_LIMIT = 250.001

[JOINT_2]
TYPE = LINEAR
HOME = 250.0
MIN_LIMIT = 0.0
MAX_LIMIT = 250.001
MAX_VELOCITY = 23.75
MAX_ACCELERATION = 750.0
STEPGEN_MAXACCEL = 937.5
SCALE = 320.0
FERROR = 1
MIN_FERROR = .25
HOME_OFFSET = 250.000000
HOME_SEARCH_VEL = 5.000000
HOME_LATCH_VEL = 1.562500
HOME_SEQUENCE = 0

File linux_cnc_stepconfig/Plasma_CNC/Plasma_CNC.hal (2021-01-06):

# Generated by stepconf 1.1 at Tue Oct 20 21:39:12 2020
# If you make changes to this file, they will be
# overwritten when you run stepconf again
loadrt [KINS]KINEMATICS
loadrt [EMCMOT]EMCMOT base_period_nsec=[EMCMOT]BASE_PERIOD servo_period_nsec=[EMCMOT]SERVO_PERIOD num_joints=[KINS]JOINTS
loadrt hal_parport cfg="0 out"
loadrt stepgen step_type=0,0,0

addf parport.0.read base-thread
addf stepgen.make-pulses base-thread
addf parport.0.write base-thread

addf stepgen.capture-position servo-thread
addf motion-command-handler servo-thread
addf motion-controller servo-thread
addf stepgen.update-freq servo-thread
net spindle-cmd-rpm     <= spindle.0.speed-out
net spindle-cmd-rpm-abs <= spindle.0.speed-out-abs
net spindle-cmd-rps     <= spindle.0.speed-out-rps
net spindle-cmd-rps-abs <= spindle.0.speed-out-rps-abs
net spindle-at-speed    => spindle.0.at-speed

net xstep           => parport.0.pin-02-out
net xdir            => parport.0.pin-03-out
setp parport.0.pin-04-out-invert 1
net xstep           => parport.0.pin-04-out
setp parport.0.pin-05-out-invert 1
net xdir            => parport.0.pin-05-out
net ystep           => parport.0.pin-06-out
net ydir            => parport.0.pin-07-out
net zstep           => parport.0.pin-08-out
net zdir            => parport.0.pin-09-out
setp parport.0.pin-17-out-invert 1
net xenable         => parport.0.pin-17-out
net home-x          <= parport.0.pin-10-in-not
net home-y          <= parport.0.pin-11-in-not
net estop-ext       <= parport.0.pin-12-in-not
net home-z          <= parport.0.pin-15-in-not

setp stepgen.0.position-scale [JOINT_0]SCALE
setp stepgen.0.steplen 1
setp stepgen.0.stepspace 1
setp stepgen.0.dirhold 40000
setp stepgen.0.dirsetup 40000
setp stepgen.0.maxaccel [JOINT_0]STEPGEN_MAXACCEL
net xpos-cmd joint.0.motor-pos-cmd => stepgen.0.position-cmd
net xpos-fb stepgen.0.position-fb => joint.0.motor-pos-fb
net xstep <= stepgen.0.step
net xdir <= stepgen.0.dir
net xenable joint.0.amp-enable-out => stepgen.0.enable
net home-x => joint.0.home-sw-in

setp stepgen.1.position-scale [JOINT_1]SCALE
setp stepgen.1.steplen 1
setp stepgen.1.stepspace 1
setp stepgen.1.dirhold 40000
setp stepgen.1.dirsetup 40000
setp stepgen.1.maxaccel [JOINT_1]STEPGEN_MAXACCEL
net ypos-cmd joint.1.motor-pos-cmd => stepgen.1.position-cmd
net ypos-fb stepgen.1.position-fb => joint.1.motor-pos-fb
net ystep <= stepgen.1.step
net ydir <= stepgen.1.dir
net yenable joint.1.amp-enable-out => stepgen.1.enable
net home-y => joint.1.home-sw-in

setp stepgen.2.position-scale [JOINT_2]SCALE
setp stepgen.2.steplen 1
setp stepgen.2.stepspace 1
setp stepgen.2.dirhold 40000
setp stepgen.2.dirsetup 40000
setp stepgen.2.maxaccel [JOINT_2]STEPGEN_MAXACCEL
net zpos-cmd joint.2.motor-pos-cmd => stepgen.2.position-cmd
net zpos-fb stepgen.2.position-fb => joint.2.motor-pos-fb
net zstep <= stepgen.2.step
net zdir <= stepgen.2.dir
net zenable joint.2.amp-enable-out => stepgen.2.enable
net home-z => joint.2.home-sw-in

net estop-out <= iocontrol.0.user-enable-out
net estop-ext => iocontrol.0.emc-enable-in

net tool-number <= iocontrol.0.tool-prep-number
net tool-change-loopback iocontrol.0.tool-change => iocontrol.0.tool-changed
net tool-prepare-loopback iocontrol.0.tool-prepare => iocontrol.0.tool-prepared

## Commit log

2020-08-30 add carta gantt
    [carta_gantt.xlsx]
2020-09-13 test csv
    [carta_gantt.csv]
2020-09-17 add previous courses docs
    [1-2 - 13 STEEL HEX CAP SCREW.ipt, 1-2 HEX_1 1-8 LNG _1-4 THR_STANDOFF.ipt, 1-2 IN SCREW STEEL FLAT WASHER.ipt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]
2020-09-18 add unzipped folder
    [MAGNUM II MATERIALS LIST.xls]
2020-10-20 Parts list
    [Partes.xlsx]
2020-11-07 update part list
    [Partes.xlsx]
2020-11-28 update bought parts
    [Partes.xlsx]
2020-12-02 udpate part list
    [Partes.xlsx]
2020-12-15 add cnc linux config
    [custom.hal, custom_postgui.hal, postgui_call_list.hal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]
2020-12-15 add step_config base
    [custom.hal, custom_postgui.hal, plasma_base.hal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]
2020-12-15 modificacion en ini y hal
    En .ini borre la X extra de la linea 59
    en el hal cambio la varibles xpo yxdir por x1pos, x1dir, y cree x2dir x2pos
    no cacho porque tienes invert in los pin 4 y 5 (estos son los del motor X2), lo otro nose que hace el in 14
    existe la creacion de la variable xenable pero no yenable or zenable, pero esas si se usan despues en el codigo
    [test_plasma.hal]
2020-12-16 XYZ funcionando
    [PLASMA_AHORASIIIII.hal, custom.hal, custom_postgui.hal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]
2020-12-20 add current status ports
2021-01-04 add actual stepconfig
    [Plasma_test.hal, custom.hal, custom_postgui.hal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]
2021-01-06 replace old config files
    [Plasma_CNC.hal, custom.hal, custom_postgui.hal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]
2021-01-06 add wiring diagram
2021-06-08 change pin number for Enable & Relay
